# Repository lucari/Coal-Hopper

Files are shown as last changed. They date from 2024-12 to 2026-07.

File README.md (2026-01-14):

# Coal-Hopper
This is an Arduino based stepper motor controller for a model railway coal-hopper.

*** The board and software has been updated as more requirements were uncovered. The original files can be found under the V1 folder ***

The design is based around an Arduino Nano and a TMC2209 Silent Stepper motor controller. There are 6 general I/O pins that are used for the home & optional away microswitches, trigger input, busy output, Train detection and Conveyor control. Trimmers are used to set the speed of the hopper, length or travel (if not using Away switch) and delay time at the Away position before moving home.

Note. The 5v supply on the I/O pins comes from the Nano voltage regulator. It will not be enough to drive relays and servos. In this instance, an external power source is required.

The end-stop switches can be Normally-Open or Normally Closed types and set by configuration variables in the software. 

When a train is detected (reed switch), the conveyor motor, via a relay board, is turned on for a period of time.

When triggered by the level of coal in the hopper or the train leaving the unloading section, and after a delay, the stepper motor will move the hopper to the Away position. Once at the top and after a delay (when the hopper is emptied), the hopper will move back to the Home position. During this time, the busy output is used via a relay to disable track power in the unloading section. 

At initialisation time, the hopper is moved back to Home. If the hopper is already Home, it is moved away for a few turns and then back Home.

The Arduino will normally be powered through the Stepper Motor supply. There is a jumper provided so this can be isolated if the Arduino is connected by its USB port to a PC. This will avoid conflicting power on the Nano.

## Arduino Code
The code is held under the Arduino folder. Any changes to the connections can be made at the top of the file. The code is written 'long-hand' to make it readable and maintainable.

## Kicad Files
A Custom PCB was made for this and can be found under the Kicad folder.

Image of the PCB Front
Image of the PCB Rear

## Completed Boards
The image below shows a completed board. 

Image of PCB Built

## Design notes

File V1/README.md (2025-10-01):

# Coal-Hopper
This is an Arduino based stepper motor controller for a model railway coal-hopper.

These are the original files before the new board was created.

When triggered, the stepper motor will move the hopper to the Away position. After a delay (when the hopper is emptied), the hopper will move back to the Home position.

The design is based around an Arduino Nano and TMC2209 Silent Stepper motor controller. There are connection for end-stop switches, but only the Home switch is required. There are trigger input and busy output connections protected by opto-couplers. These can be removed if required and direct connections used instead (i.e relay / switch for input). Trimmers can be used to set the speed of the hopper, length or travel (if not using Away switch) and delay time at the Away position before moving home.

The end-stop switches can be Normally-Open or Normally Closed types and set by installing a jumper on the appropriate header. For Normally Open types, these can actually be left off but the board has space for the jumpers.

The Arduino can also be powered through the Motor supply. There is a jumper provided so this can be isolated if the Arduino is connected by its USB port to a PC. Its stops strange things happening.

## Arduino Code
The code is held under the Arduino folder. Any changes to the connections can be made at the top of the file. The code is written 'long-hand' to make it readable and maintainable.

## Kicad Files
A Custom PCB was made for this and can be found under the Kicad folder.

Image of the PCB Front
Image of the PCB Rear

## Completed Boards
The images below show completed boards. 
This one has the Opto-Couplers installed.

Image of PCB with Opto-Couplers

This one has direct links and can be used for relay contacts or switch. It also has headers for the LEDs so they can be mounted remotely.

Image of PCB with Opto-Couplers

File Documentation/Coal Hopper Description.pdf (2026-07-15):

# Coal Hopper

# Design Notes

## Version 1.0

Coal Hopper Design v1.0

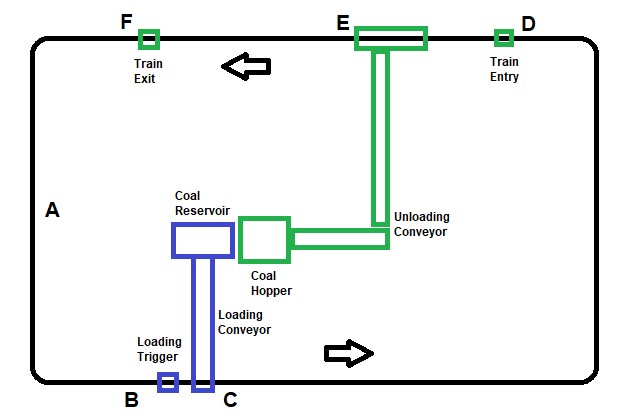
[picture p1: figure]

Page 1 of 9

## Overview

The Coal Wagon exhibition layout of the Bracknell Railway Society runs a continuous loop of trains, pulling several coal wagons, that are filled and emptied automatically. A simplified layout is shown below.

The train, pulling a number of coal wagons, travels anti-clockwise starting empty at point A. Each wagon has a small magnet fitted and when it passed over the loading trigger reed switch at point B, it causes the train to stop after a short delay, with the wagon under the loading chute C. This also starts the loading conveyor to move coal from the reservoir into a loading bucket. When this fills to a certain amount, the bucket tips and dispenses the coal down the chute into the wagon. A tilt switch on the bucket stops the conveyor and after a short delay, restarts the train. As each wagon passes the loading trigger, the process repeats. When all the wagons are loaded, the train continues around the loop.

When the train reaches train entry point D, the unloading conveyor is started. As the wagons reach point E, the coal is automatically unloaded through the bottom of the wagon. The coal is moved up the unloading conveyors to the coal hopper.

Once the train reaches the train exit point F, and after a short delay, the unloading conveyor is turned off. The coal hopper is raised up the tower and is tipped into the coal reservoir. It then returns to the base.

The train reaches point A again and the cycle repeats itself.

This document covers the green unloading part of the layout and how the reservoir of coal in the loading tower is replenished.

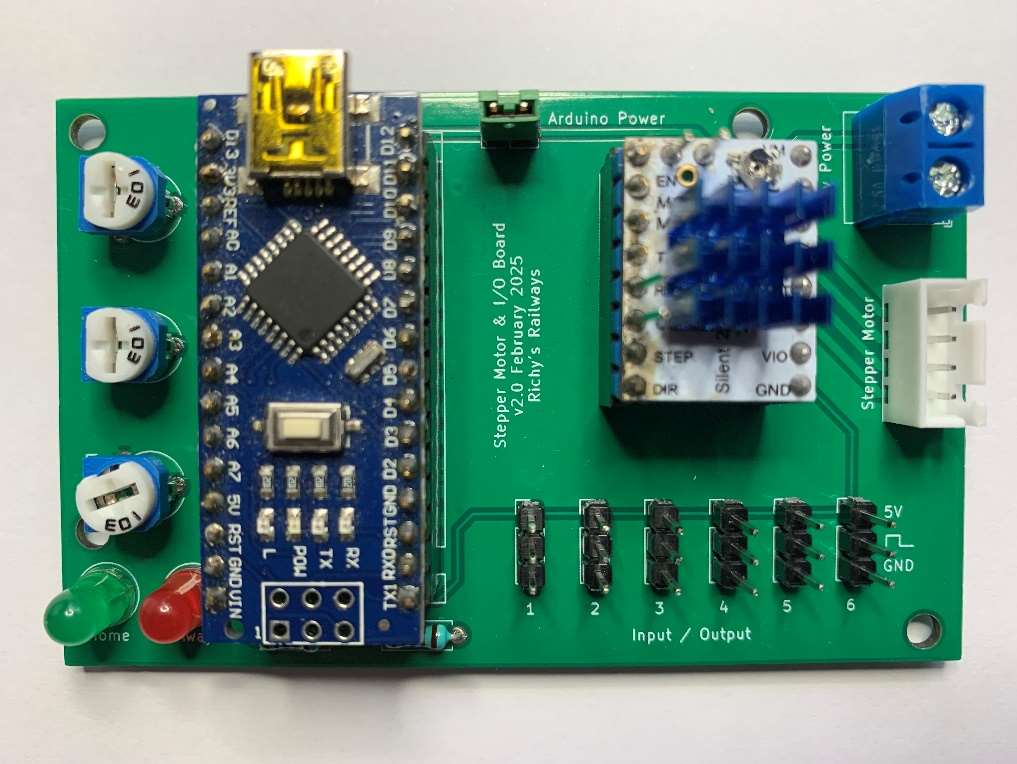
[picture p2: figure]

Page 2 of 9

## Hardware

A custom PCB has been designed, based on an Arduino microcontroller that detects the train location and moves a coal hopper lift using a stepper motor. The final version of the board is shown below.

The main part of the board is the Arduino Nano. The USB interface on this is used only for programming and debugging. In normal operation, it takes power from the 12V supply used for the Stepper Motor.

The jumper to the right of the Arduino can be used to disconnect the 12V supply. When the Arduino is powered through its USB connector, the jumper should be removed to avoid power supply conflicts and protect the host computer. In normal; operation with no USB connection, the jumper should be fitted.

The stepper motor driver is a Silent_2209 board. This drives the stepper motor in 1/8 micro steps with very little noise compared to a normal driver board.

The 3 variable resisters or trimmers are used to tune the configuration of the board. These are:

- Delay – the time to wait before moving to the home or away position.
- Speed – How fast the stepper motor turns.
- Length – The number of turns the motor will take to move from home to away.

Page 3 of 9

There are 6 I/O interfaces on the board. These are used as follows:

1. Home switch (input) – This is connected to a ‘normally-open’ microswitch.
2. Away switch (input) – This is currently not fitted.
3. Conveyor motor control (output) – This drives a relay board.
4. Train entry sensor (input) – This is a small reed switch.
5. Train exit sensor (input) – This is a small reed switch.
6. Busy / Track power (output) – This drives a relay board.

The two LEDs display different patterns depending on what state the board is in.

The Green LED shows the ‘Home’ state, and the Red LED shows the ‘Away’ state. These will light and flash in different combinations to show what function the board is performing.

All the above will be covered in detail within the document.

Page 4 of 9

## Software Description

The Arduino code is written in ‘C’ and can be found in the GitHub repository at https://github.com/lucari/Coal-Hopper, along with the PCB design files. The code should be used with the following description to understand how it works.

The software design is based on a finite-state-machine model. The code will be in one state until some trigger causes it to perform an action and move to a new state. The possible states are: Initialise, Home, Move-Away, Away, Move-Home and Error.

Initialise

Once the Arduino starts up and has performed its local setup functions, it is in the Initialise state (InitialiseHopper function). It flashes the LEDs to show test they are working and reads the trimmer pots to get the tuneable values.

Because the power could have been removed at any time, the location of the hopper is checked. If the home switch is active (hopper is home), then it is moved away for a number of turns and then returned home. If the Home switch is inactive (hopper is away), the hopper is returned home. This checks that the home switch is working correctly. If the state of the home switch does not change after a number of turns, the program enters the Error state. If the home switch does change correctly, the program enters the Home state.

Home

This is the state that the program will be in most of the time (WaitForHopperTrigger function). The stepper motor is disabled during this time to save power. While it is idle, it will check the trimmer pots every 15 seconds and update the tuneable values.

The function is waiting for one of two triggers to occur. The ‘Train Entry’ trigger (trainSensorPin) going low cause the unloading conveyors to start. This is handled by taking the conveyorMotorPin pin low, which is connected to an external relay board. It also starts a 60 second time that is checked within the loop. When this expires, the pin is raised and stopping the conveyors. The state is not changed by this event.

When the ‘Train Exit’ trigger (bucketFullSensorPin) goes low, the idle loop is exited. The program will wait for the number of seconds defined by the trim pots. This is to ensure that the unloading conveyors are empty and the train has cleared the section. The track power is then turned off by taking the hopperBusyPin pin low. This is connected to an external relay board. It also stops the unloading conveyors if they were running. The program enters the Move-Away state.

Page 5 of 9

Move-Away

This is the transient state where the hopper is being moved from the home (lower) to the away (raised) position (MoveHopperToAway function). The stepper motor board is driven by setting the direction pin high and the enable pin low. The step pin is pulsed by setting it high, wait, low, and wait. The wait time is set by the trimmer pots, and the optimum value was found to be 200uS. At the start and end of the run, the delay is doubled to slow it down.

It was found that a steady stream of pulses works best. When the debug messages were included, the stepper produced a knocking sound at each turn. So, these have been commented out.

The stepper motor is moved until the away switch is reached (if fitted) or the number of turns specified by the trim pots is reached. The number of turns required on the current setup is 53. The driver board is set for 1/8 steps so a full turn will require 8 * 200 = 1600 pulses.

When the endpoint is reached, the stepper motor is disabled to save power. The program enters the Away state.

Away

This is the transient state when the hopper is at the highest point and is emptying the coal into the reservoir (WaitForHopperToEmpty function). It simply waits for the number of seconds defined by the trimmer pots. The value of 10 seconds seems to work best.

Once the timer expires, the program enters the Move-Home state.

Move-Home

This is the transient state where the hopper is being moved from the away (raised) to the home (lower) position (MoveHopperToHome function). It operates in the same manner as the Move-Away state, except the direction pin is set low. The Home switch will always be fitted so this is the trigger that will stop the hopper moving. Once reached, the program enters the Home state.

If the number of turns is exceeded, the program enters the Error state.

Error

When something unexpected happens, the program enters the Error state and halts processing.

Page 6 of 9

## LED Patterns / Debugging

The two LEDs show the current state and functions of the program.

Home Green | Away Red | Meaning
On On Off | On Off Off | Initialise / Start up sequence
On Off | Off On | Error state. Alternates every second
On | Off | Home state – waiting for trigger
On | Fast | Home state – delay before moving away (fast flash Away LED)
On | Flash | Move-Away state – alternate Away LED each turn
Off | On | Away state – waiting for timeout
Flash | On | Move-Home – alternate Home LED each turn

The USB port of the Arduino can also be used to view debug messages from the program. The Arduino Power jumper should be removed from the board to avoid conflicts. A USB lead should be connected to a computer and the Arduino IDE started. The Serial Monitor can be found under the Tools menu. The serial port speed should be set to 115200.

InitialiseHopper: Start
InitialiseHopper: Hopper away from home position. Moving to home.
InitialiseHopper: Full turn home complete. InitialiseHopper: Full turn home complete. InitialiseHopper: Full turn home complete. InitialiseHopper: Hopper successfully moved home. WaitForHopperTrigger: At start, waiting 5 seconds. WaitForHopperTrigger: Waiting for trigger to move. WaitForHopperTrigger: Setting defaultDelay (Speed) to 206 WaitForHopperTrigger: Setting turnsToAway (Length) to 53 WaitForHopperTrigger: Setting awayWaitTime (Delay) to 10146

Page 7 of 9

## Connectivity

The connections to the board are shown below. It should be noted that the 5V supply is fed from the Arduino on-board regulator and can only provide limited current. It cannot be used to drive relay boards or servos. The signal side (opto isolator) connection is ok to use 5V, but not the relay side (JD-VCC).

These connections are directly connected.

I/O 1 | Gnd | Black | Home switch direct on green and black wire.
| Sig | Green
| +5V | -
I/O 2 | Gnd | - | Not used
| Sig | -
| +5V | -

These connections are through the patch block.

I/O 3 | Gnd | - | Unload conveyor relay board. Just uses +5V and signal. Relay board must use external
| | Brown | power for relay side (JD-VCC) Sig
| +5V | Red
I/O 4 | Gnd | Orange | Reed switch. Just uses Sig and Gnd.
| Sig | Yellow
| +5V | Green
I/O 5 | Gnd | Blue | Reed switch. Just uses Sig and Gnd.
| Sig | Violet
| +5V | Grey
I/O 6 | Gnd | - | Track Power isolator relay board. Just uses +5V and signal. +5V is common with I/O 3. Relay board must use external power for relay side (JD-VCC)
| Sig | White
| +5V | Black

Page 8 of 9

## Stepper Motor Wiring

It has been found that there are two type of stepper motor interfaces and require different cables. If the wrong cable is used, the stepper motor will judder and not turn.

4 pin (driver) | 6 pin type 1 | 6 pin type 2
| A2 | A2
A2 | - | -
A1 | A1 | B1
B1 | B1 | A1
B2 | - | -
| B2 | B2

The pins on the stepper motor should be checked for connectivity to determine the correct cable.

*** The stepper motor type in the current installation is unknown ***

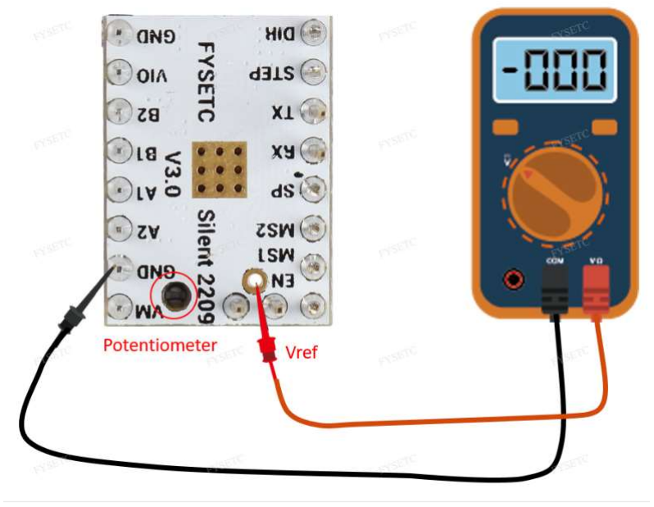
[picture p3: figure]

Page 9 of 9

## Stepper Motor Current Limit

The current limit must be set on the stepper driver board, or it will consume high current and could impact the wiring. The current is set by applying power to the VM and Ground pins and then measuring the voltage on the Vref pin. The current limit can be adjusted using the trim pot. The stepper motor must not be connected to the board, or it will cause damage.

The current is defined as Vref * 0.71. The board is set to 0.6A with a Vref of 0.85V

The weblink https://wiki.fysetc.com/docs/Silent2209 gives full details of the stepper motor driver board.

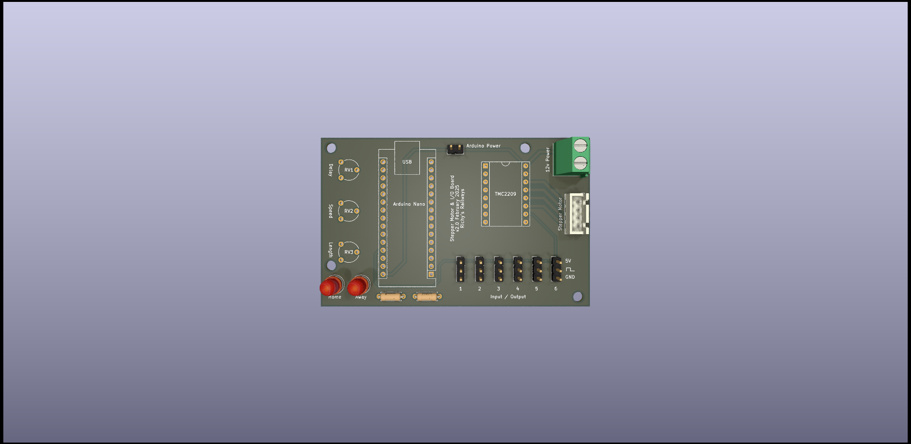
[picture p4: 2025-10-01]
Kicad/Coal-Hopper-V2.png

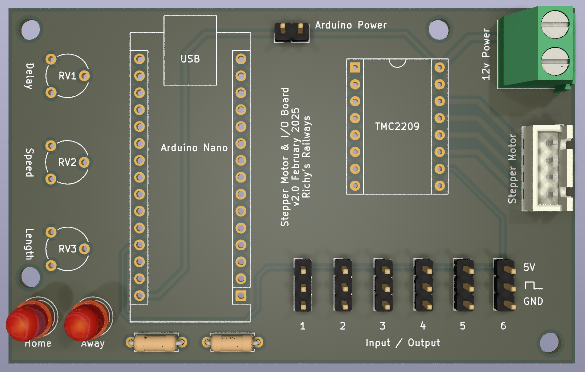
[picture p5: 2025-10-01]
Kicad/Coal-Hopper-V2-cropped.png

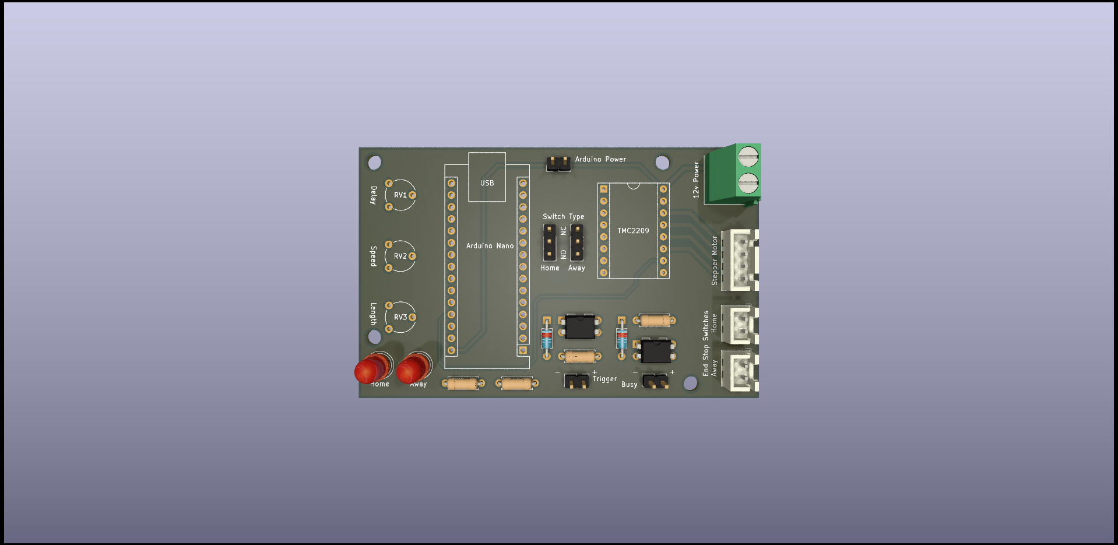
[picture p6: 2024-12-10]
V1/Kicad/Coal-Hopper.png

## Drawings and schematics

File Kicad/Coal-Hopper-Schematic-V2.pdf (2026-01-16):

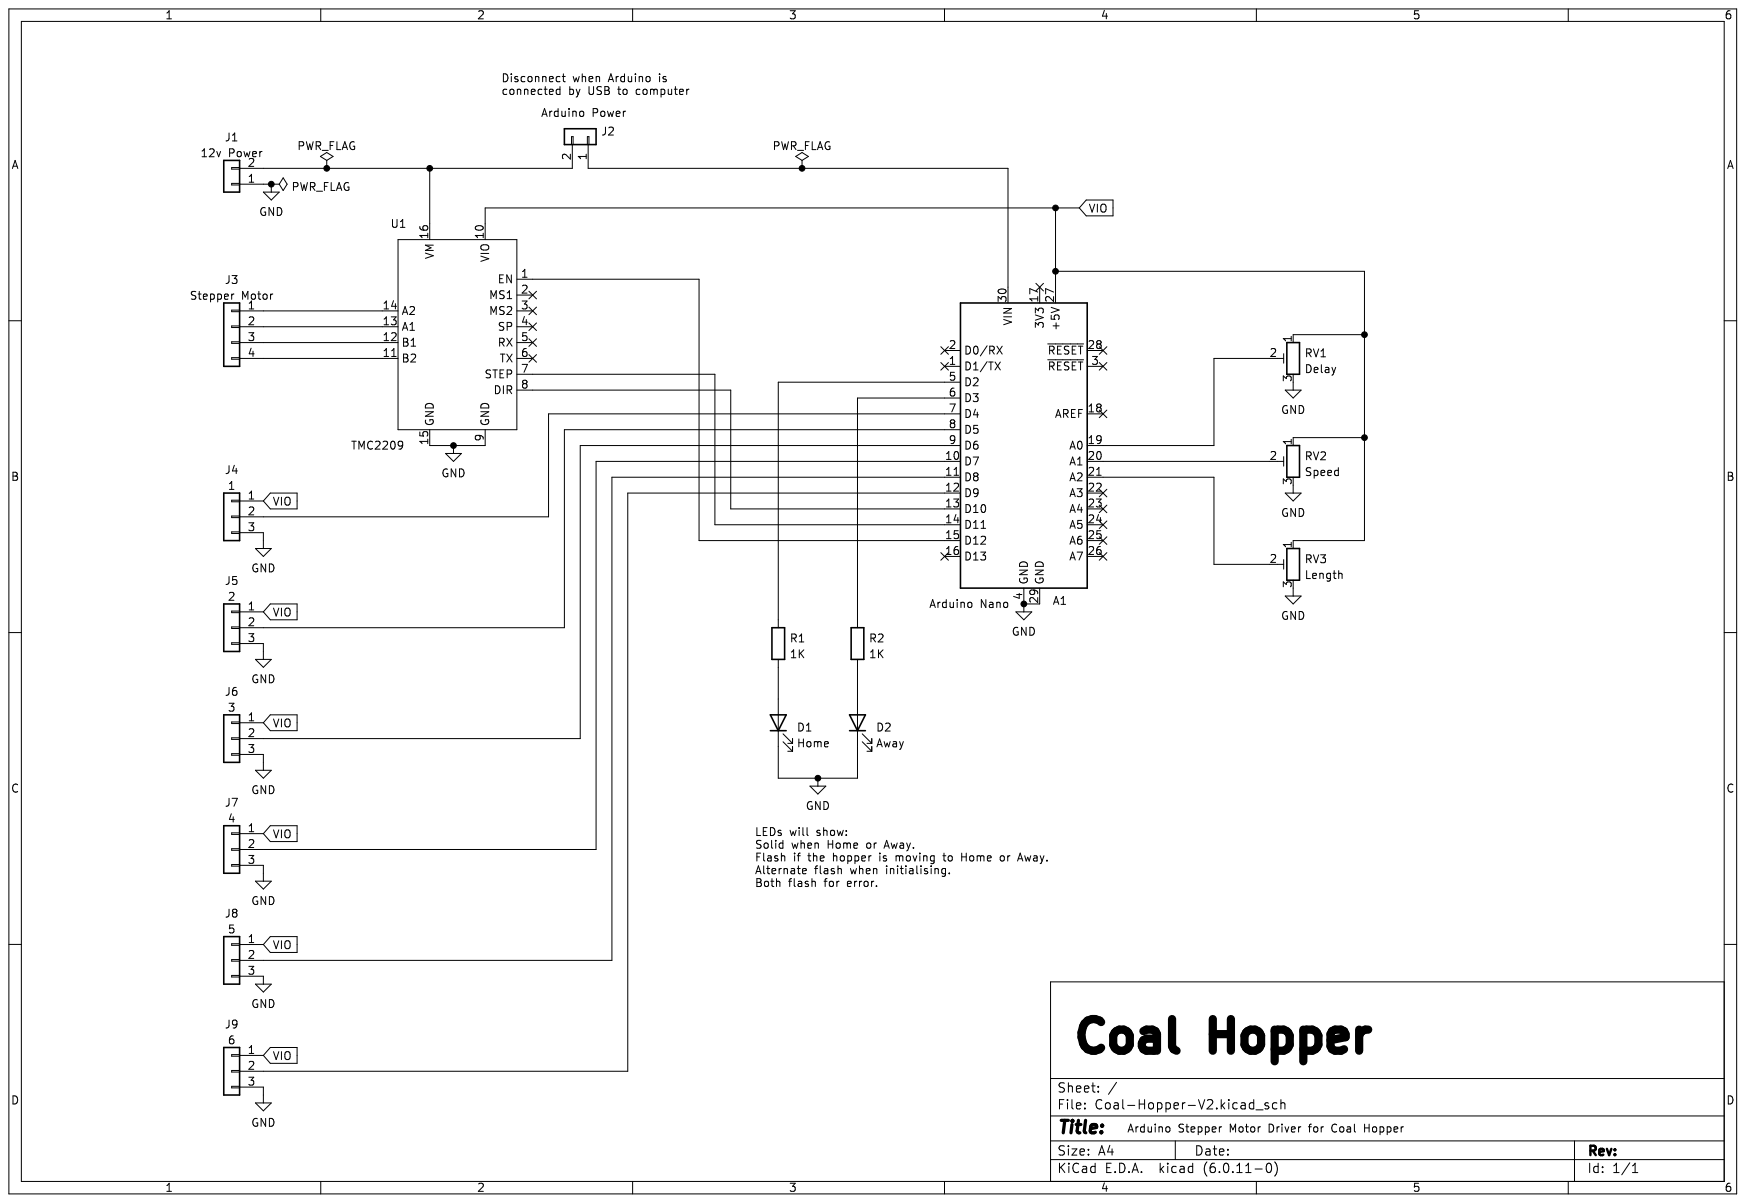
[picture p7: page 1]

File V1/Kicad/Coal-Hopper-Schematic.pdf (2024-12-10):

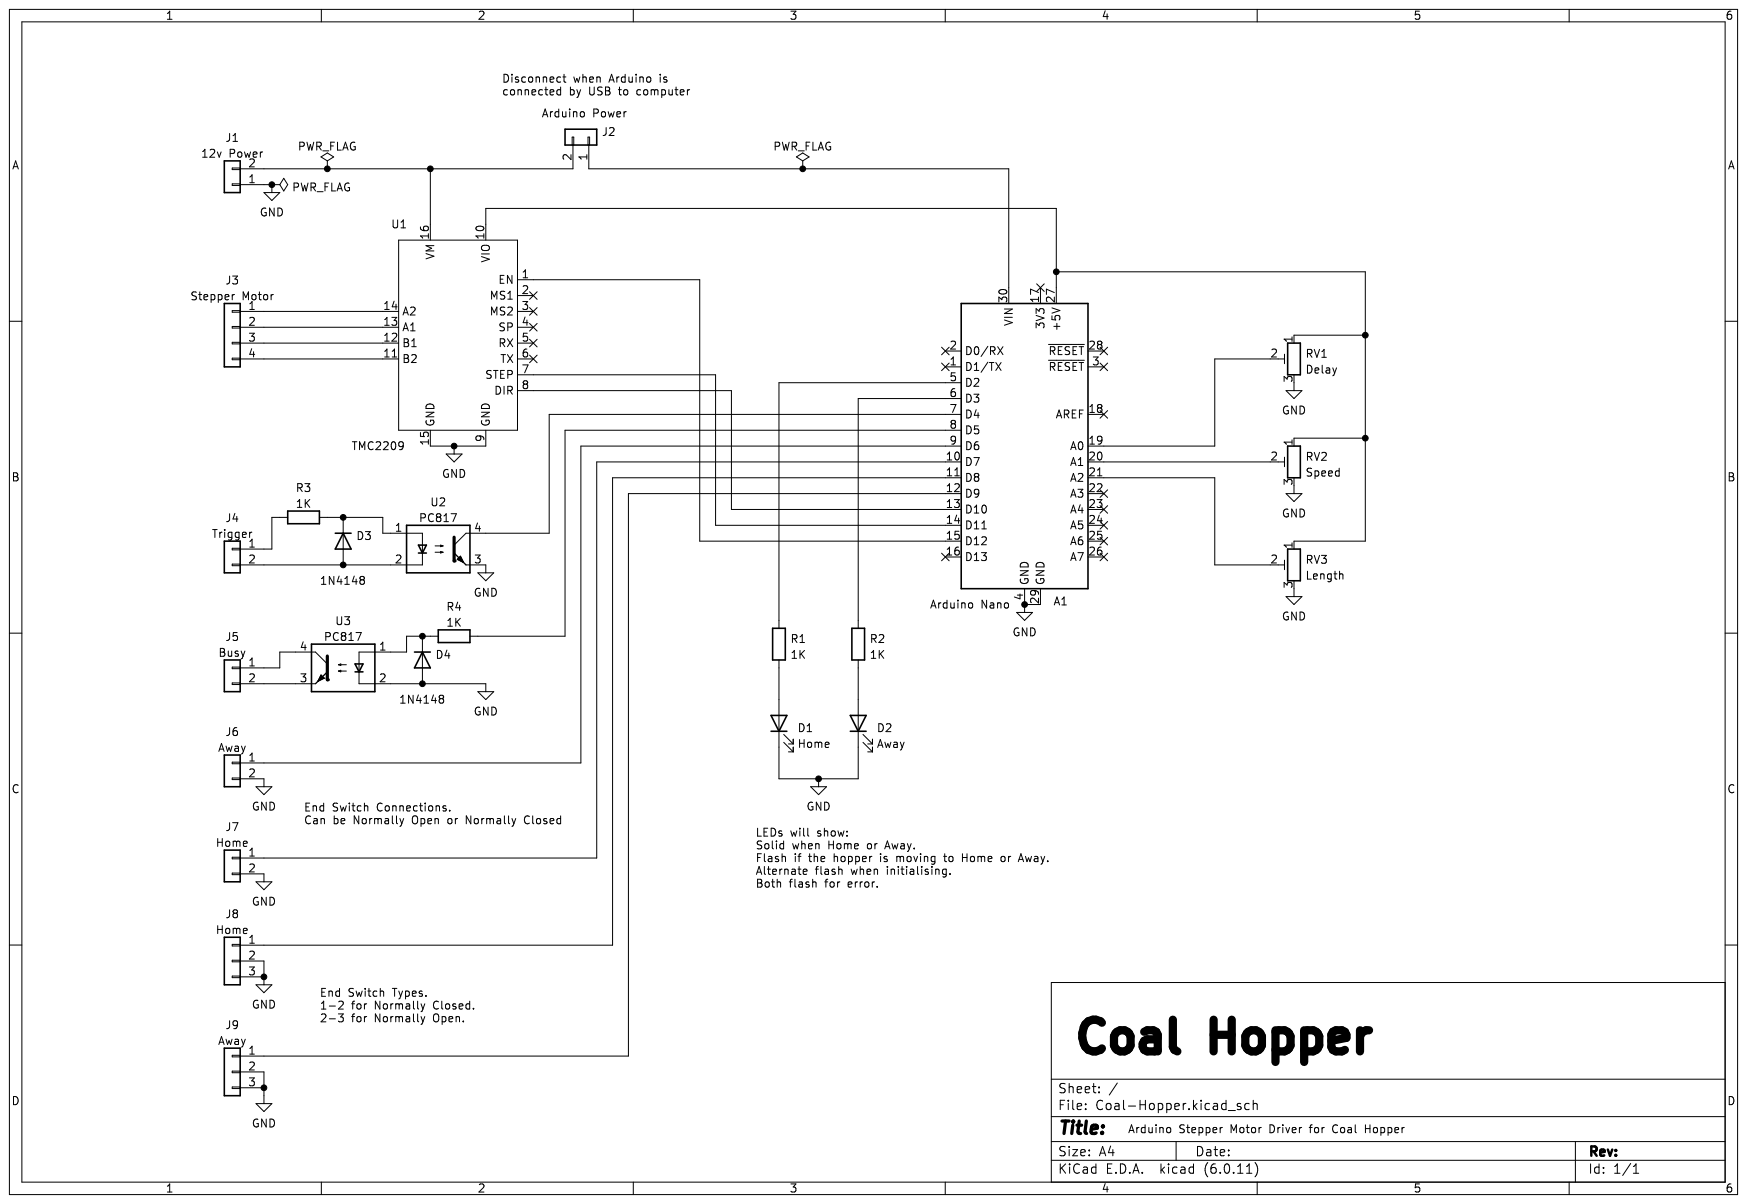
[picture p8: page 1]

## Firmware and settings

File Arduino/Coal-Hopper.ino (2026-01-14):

// Coal Hopper Stepper Functions
//
// Arduino code to control the movement of a coal hopper for a model railway layout.
// 
// Version History
//
// v1.0 07/11/2024 First draft
// v2.0 10/11/2024 Some minor tweaks
// v3.0 20/11/2024 Added Analog inputs for Speed, Wait and Length. 
// v4.0 10/12/2024 Reconfigure for new PCB
// v5.0 07/07/2025 Reconfigure for updated PCB
// v6.0 07/11/2025 Added delay on trigger to allow coal to clear conveyor before moving bucket.
//


//======== The following can be changed to suit the setup ===========================

// Define stepper motor connections
#define homeLEDPin 2
#define awayLEDPin 3

#define homePin 4
#define awayPin 5
#define conveyorMotorPin 6
#define trainSensorPin 7
#define bucketFullSensorPin 8
#define hopperBusyPin 9

#define directionPin 10
#define stepPin 11
#define enablePin 12


// Define Analog pins
#define delayAnalog A0
#define speedAnalog A1
#define lengthAnalog A2

// Define steps per revolution and size of travel
#define stepsPerRevolution (8 * 200)

// We always use the home switch so this is fixed for 500mm
#define MAX_TURNS_TO_HOME 55

#define DEFAULT_TURNS_TO_AWAY 40
#define MIN_TURNS_TO_AWAY 35
#define MAX_TURNS_TO_AWAY 55

// Specify if Home switch is Normally Open or Closed
#define DEFAULT_HOME_OPEN true 

// Specify if Away switch is Normally Open or Closed
#define DEFAULT_AWAY_OPEN true 

// Specify if Hopper Triger is Active High or Low 
#define TRIGGER_ACTIVE_HIGH false 

// Specify if Train Sensor is Active High or Low 
#define TRAINSENSOR_ACTIVE_HIGH false

// Specify the default delay between steps in uS (will be double this) amd the max & min
#define DEFAULT_DELAY 200
#define MIN_DELAY 100
#define MAX_DELAY 300

// Specify the default wait time in mS at the top
#define DEFAULT_WAIT 10000
#define MIN_WAIT 5000
#define MAX_WAIT 15000


//===================================================================================


// Define the states the hopper can be in
#define HOPPER_INIT 0
#define HOPPER_HOME 1
#define HOPPER_MOVE_AWAY 2
#define HOPPER_AWAY 3
#define HOPPER_MOVE_HOME 4
#define HOPPER_ERROR 255


// Define if the motor is going to Home or Away
#define STEP_AWAY 0
#define STEP_HOME 1


// Set state to init
int hopperState = HOPPER_INIT;

// Set delay to 200uS
int defaultDelay = DEFAULT_DELAY;

// Set the default distance to away until we read the triimers
int turnsToAway = DEFAULT_TURNS_TO_AWAY;

// Set the time to wait at the top before returning / time after trigger that we wait for before moving the hopper.
int awayWaitTime = DEFAULT_WAIT;

// Set a flag to ignore trimmers if all analog inputs are grounded
bool checkTrimmers = true;

// Variables to specify if home and away switch are normally open or closed. 
bool awaySwitchNO = DEFAULT_AWAY_OPEN;
bool homeSwitchNO = DEFAULT_HOME_OPEN;

// Conveyor will run for 60 seconds
#define CONVEYOR_RUN_TIME 60000L
unsigned long stopConveyorTime = 0L;

// Declare functions
void InitialiseHopper();
void WaitForHopperTrigger();
void MoveHopperToAway();
void WaitForHopperToEmpty();
void MoveHopperToHome();
void HopperError();
bool IsHomeActive();
bool IsAwayActive();
bool IsTriggerActive();

void setup() 
{
  // Declare pins as output:
  pinMode(stepPin, OUTPUT);
  pinMode(directionPin, OUTPUT);
  pinMode(enablePin, OUTPUT);
  pinMode(hopperBusyPin, OUTPUT);
  pinMode(conveyorMotorPin, OUTPUT);
  pinMode(homeLEDPin, OUTPUT);
  pinMode(awayLEDPin, OUTPUT);

  // and the inputs with pullups
  pinMode(homePin, INPUT_PULLUP);
  pinMode(awayPin, INPUT_PULLUP);
  pinMode(trainSensorPin, INPUT_PULLUP);
  pinMode(bucketFullSensorPin, INPUT_PULLUP);

  // Disable the controller for now
  digitalWrite(enablePin, HIGH);

  // Show we are busy and converyor off (relays active low)
  digitalWrite(hopperBusyPin, LOW);
  digitalWrite(conveyorMotorPin, HIGH);

  // Clear the LEDs
  digitalWrite(homeLEDPin, LOW);
  digitalWrite(awayLEDPin, LOW);

  // Configure Serial for debugging
  Serial.begin(115200);

  // Give it time to settle
  delay(500);

  // Set the initial state to init.
  hopperState = HOPPER_INIT;
}

void loop()
{
  // Loop around and call the appropriate function delepnding on the state.
  if (hopperState == HOPPER_INIT)
  {
    // First thing is to initialise and home the hopper
    InitialiseHopper();
  }
  else if (hopperState == HOPPER_HOME)
  {
    // Hopper is Home, wait to be told to move the hopper
    WaitForHopperTrigger();
  }
  else if (hopperState == HOPPER_MOVE_AWAY)
  {
    // Move the hopper to the away point
    MoveHopperToAway();
  }
  else if (hopperState == HOPPER_AWAY)
  {
    // Hopper is away, wait for it to empty.
    WaitForHopperToEmpty();
  }
  else if (hopperState == HOPPER_MOVE_HOME)
  {
    // Move the hopper back home
    MoveHopperToHome();
  }
  else
  {
    // Something has broken. Stop
    HopperError();
  }
}



bool
IsTriggerActive()
{
  // Check to see if its active high or low
  if (TRIGGER_ACTIVE_HIGH)
  {
    // It is active high
    if (digitalRead(bucketFullSensorPin) == HIGH)
    {
      return(true);
    }
    else
    {
      return(false);
    }
  }
  else
  {
    // It is active low
    if (digitalRead(bucketFullSensorPin) == LOW)
    {
      return(true);
    }
    else
    {
      return(false);
    }    
  }
}

bool
IsTrainSensed()
{
  // Check to see if its active high or low
  if (TRAINSENSOR_ACTIVE_HIGH)
  {
    // It is active high
    if (digitalRead(trainSensorPin) == HIGH)
    {
      return(true);
    }
    else
    {
      return(false);
    }
  }
  else
  {
    // It is active low
    if (digitalRead(trainSensorPin) == LOW)
    {
      return(true);
    }
    else
    {
      return(false);
    }    
  }
}

//
// Is Home Switch Active
//
// Checks the state of the home switch.
// Caters for Normally Open and Normally Closed type switches
// Switch is between pin and ground with pullup enabled
//
bool
IsHomeActive()
{
  if (homeSwitchNO)
  {
    // Home switch is normally open
    if (digitalRead(homePin) == LOW)
    {
      // Active low so switch is pressed (NO)
      return(true);
    }
    else
    {
      // Its high, so not switched (NO)
      return(false);
    }
  }
  else
  {
    // Home switch is normally closed
    if (digitalRead(homePin) == LOW)
    {
      // Active low so its not switched (NC)
      return(false);
    }
    else
    {
      // Its high, so switch is pressed (NC)
      return(true);
    }
  }
}

//
// Is Away Switch Active
//
// Checks the state of the away switch.
// Caters for Normally Open and Normally Closed type switches
// Switch is between pin and ground with pullup enabled
//
bool
IsAwayActive()
{
  if (awaySwitchNO)
  {
    // Away switch is normally open
    if (digitalRead(awayPin) == LOW)
    {
      // Active low so switch is pressed (NO)
      return(true);
    }
    else
    {
      // Its high, so not switched (NO)
      return(false);
    }
  }
  else
  {
    // Away switch is normally closed
    if (digitalRead(awayPin) == LOW)
    {
      // Active low so its not switched (NC)
      return(false);
    }
    else
    {
      // Its high, so switch is pressed (NC)
      return(true);
    }
  }
}


//
// Move Stepper
//
// Move the stepper one step to Home or Away and wait.
//
void
MoveStepper(int stepDirection, int stepDelay)
{
  // Enable the board
  digitalWrite(enablePin, LOW);

  // Check direction
  if (stepDirection == STEP_AWAY)
  {
    // Move to Away point
    digitalWrite(directionPin, HIGH);
  }
  else
  {
    // Move to Home point
    digitalWrite(directionPin, LOW);
  }
  
  // Pulse line high
  digitalWrite(stepPin, HIGH);

  // Wait for passed time (uS)
  delayMicroseconds(stepDelay);
  
  // Pulse line low
  digitalWrite(stepPin, LOW);

  // Wait for passed time (uS)
  delayMicroseconds(stepDelay);
 
}


//
// Initialise Hopper
//
// At startup, move hopper back to home position.
// If the hopper is already home, move away and back to confirm switch.
// If the Home switch does not activate after a number of turns, move to ERROR state.
// If ok, set the HOME state.
//
void
InitialiseHopper()
{
  bool ledsAreOn = false;
  
  Serial.print(F("InitialiseHopper: Start\n"));

  // Flash the LEDs at the start so we dont move the motor as soon as the power is applied

  digitalWrite(homeLEDPin, HIGH);
  digitalWrite(awayLEDPin, HIGH);
  delay(2000);
  digitalWrite(homeLEDPin, HIGH);
  digitalWrite(awayLEDPin, LOW);
  delay(2000);
  digitalWrite(homeLEDPin, LOW);
  digitalWrite(awayLEDPin, LOW);
  delay(2000);

  // Check to see if all the analog inputs are grounded. If so, ignore them and use defaults
  if (analogRead(delayAnalog) == 0 && analogRead(speedAnalog) == 0 && analogRead(lengthAnalog) == 0)
  {
    Serial.print(F("InitialiseHopper: All trimmers at 0 so using defaults.\n"));

    Serial.print(F("WaitForHopperTrigger: Setting defaultDelay (Speed) to "));
    Serial.print(defaultDelay);
    Serial.print(F(" \n"));

    Serial.print(F("WaitForHopperTrigger: Setting turnsToAway (Length) to "));
    Serial.print(turnsToAway);
    Serial.print(F(" \n"));

    Serial.print(F("WaitForHopperTrigger: Setting awayWaitTime (Delay) to "));
    Serial.print(awayWaitTime);
    Serial.print(F(" \n"));

    
    checkTrimmers = false;
  }


 
  // First check if the home switch is already active (low)
  if (IsHomeActive() == true)
  {
    Serial.print(F("InitialiseHopper: Hopper at home position. Moving away.\n"));
    // Yes, move away a number of steps (4 rotations) to see if it goes high.
    for (int i = 0; i < 4; i++)
    {

      // Flash the LEDs at the same time
      if (ledsAreOn == true)
      {
        // Its on so turn it off
        ledsAreOn = false;
        digitalWrite(homeLEDPin, LOW);
        digitalWrite(awayLEDPin, LOW);
      }
      else
      {
        // Its off so turn it on
        ledsAreOn = true;
        digitalWrite(homeLEDPin, HIGH);
        digitalWrite(awayLEDPin, HIGH);
      }
      
      for (int j = 0; j < stepsPerRevolution; j++)
      {
        // Move at half speed.
        MoveStepper(STEP_AWAY, defaultDelay*2);        
      }
      Serial.print(F("InitialiseHopper: Full turn away complete.\n"));
    }

    // Check again
    if (IsHomeActive() == true)
    {
      // Its still active so hasn't moved. Go to Error state
      Serial.print(F("InitialiseHopper: *** Error *** Hopper failed to move away.\n"));
      hopperState = HOPPER_ERROR;
      return;
    }
  }

  // If we are here, the home switch must be inactive. Try and move it to Home.
  Serial.print(F("InitialiseHopper: Hopper away from home position. Moving to home.\n"));
  for (int i = 0; i < MAX_TURNS_TO_HOME; i++)
  {

    // Flash the LEDs at the same time
    if (ledsAreOn == true)
    {
      // Its on so turn it off
      ledsAreOn = false;
      digitalWrite(homeLEDPin, LOW);
      digitalWrite(awayLEDPin, LOW);
    }
    else
    {
      // Its off so turn it on
      ledsAreOn = true;
      digitalWrite(homeLEDPin, HIGH);
      digitalWrite(awayLEDPin, HIGH);
    }
    
    for (int j = 0; j < stepsPerRevolution; j++)
    {
      // Check to see if we have hit the home stop
      if (IsHomeActive() == true)
      {
        // Yes. Init is complete
        Serial.print(F("InitialiseHopper: Hopper successfully moved home.\n"));
        hopperState = HOPPER_HOME;
        return;
      }
      
      // Move at half speed.
      MoveStepper(STEP_HOME, defaultDelay*2);        
    }
    Serial.print(F("InitialiseHopper: Full turn home complete.\n"));
  }

  // If we reach here, it means we have not found the Home switch. So throw an error
  Serial.print(F("InitialiseHopper: *** Error *** Hopper failed to move home.\n"));
  hopperState = HOPPER_ERROR;
}


//
// Wait For Hopper Trigger (Home)
//
// Hopper is at home position and waiting for trigger to move.
// When triggered, move to MOVE_AWAY state
//
void
WaitForHopperTrigger()
{
  int count;
  long longScratch1;
  long longScratch2;
  long longScratch3;
  
  // Disable the stepper controller to save power
  digitalWrite(enablePin, HIGH);

  // Turn on Home LED and AWAY off
  digitalWrite(homeLEDPin, HIGH);
  digitalWrite(awayLEDPin, LOW);

  // At start, wait 5 seconds before doing anything
  Serial.print(F("WaitForHopperTrigger: At start, waiting 5 seconds.\n"));
  delay(5000);

  // Show we are not busy
  digitalWrite(hopperBusyPin, HIGH);
  

  Serial.print(F("WaitForHopperTrigger: Waiting for trigger to move.\n"));

  // Keep track of how long we wait so we can read trimmers. First time read them at the start
  count = 0;
  
  // Check the trigger
  while(IsTriggerActive() == false)
  {
    // Check the train sensor
    if (IsTrainSensed())
    {
      // Yes, start the conveyor and start timer
      Serial.print(F("WaitForHopperTrigger: Train Sensed, Starting Conveyor.\n"));
      
      digitalWrite(conveyorMotorPin, LOW);
      stopConveyorTime = millis() + CONVEYOR_RUN_TIME;
    }

    // Check conveyor timer
    if (stopConveyorTime > 0L)
    {
      if (millis() > stopConveyorTime)
      {
        Serial.print(F("WaitForHopperTrigger: Conveyor Timer expired, Stopping Conveyor.\n"));
        
        digitalWrite(conveyorMotorPin, HIGH);
        stopConveyorTime = 0L;
      }
    }
    // Sleep for 1/100 second if not
    delay(10);
    --count;
    
    // Timed out for trimmers if enabled
    if (checkTrimmers && count < 0)
    {
      // Set to wait 15 seconds before reading again
      count = 1500;
      
      // Set delay time to govern speed of hopper (Speed Trimmer)
      // Bigger than int values so work it out long hand or it doesnt work very well.
      longScratch1 = MAX_DELAY - MIN_DELAY;
      longScratch2 = longScratch1 * analogRead(speedAnalog);
      longScratch3 = longScratch2 / 1024L;
      defaultDelay = int(longScratch3) + MIN_DELAY;
      Serial.print(F("WaitForHopperTrigger: Setting defaultDelay (Speed) to "));
      Serial.print(defaultDelay);
      Serial.print(F(" \n"));

      // Set how many turns to away (Length Trimmer)
      turnsToAway = (((MAX_TURNS_TO_AWAY - MIN_TURNS_TO_AWAY) * analogRead(lengthAnalog)) / 1024) + MIN_TURNS_TO_AWAY;
      Serial.print(F("WaitForHopperTrigger: Setting turnsToAway (Length) to "));
      Serial.print(turnsToAway);
      Serial.print(F(" \n"));

      // Set the time to wait at the top before returning. (Delay Trimmer)
      // Bigger than int values so work it out long hand or it doesnt work.
      longScratch1 = MAX_WAIT - MIN_WAIT;
      longScratch2 = longScratch1 * analogRead(delayAnalog);
      longScratch3 = longScratch2 / 1024L;
      awayWaitTime = int(longScratch3) + MIN_WAIT;

      Serial.print(F("WaitForHopperTrigger: Setting awayWaitTime (Delay) to "));
      Serial.print(awayWaitTime);
      Serial.print(F(" \n"));
      
    }
  }

  // We have been triggered. Wait before moving. Flash Away LED fast
  Serial.print(F("WaitForHopperTrigger: Got Trigger, Waiting before moving away.\n"));
  Serial.print(F("WaitForHopperTrigger: Sleeping for "));
  Serial.print(awayWaitTime);
  Serial.print(F(" mS\n"));

  // Turn off Away LED
  digitalWrite(awayLEDPin, LOW);

  // Wait for the defined time and toggle the Away LED every 200mS to show something is happening
  count = 0;
  while (count < awayWaitTime)
  {
    delay(200);
    digitalWrite(awayLEDPin, HIGH);
    delay(200);
    digitalWrite(awayLEDPin, LOW);
    count += 400;
  }
  // Turn off Away LED
  digitalWrite(awayLEDPin, LOW);

  // Now we can move the hopper
  Serial.print(F("WaitForHopperTrigger: Got Trigger, state changed to Move-Away.\n"));

  // Turn off Home LED
  digitalWrite(homeLEDPin, LOW);

  // Show we are busy
  digitalWrite(hopperBusyPin, LOW);

  // Stop the conveyor & timer
  digitalWrite(conveyorMotorPin, HIGH);
  stopConveyorTime = 0L;

  hopperState = HOPPER_MOVE_AWAY;
}



//
// Move Hopper to Away position
//
// Trigger has been received and hopper is moved away.
// The speed to of the hopper is ramped up at the start and slowed down as the end.
// Hopper will stop when it hits the Away switch.
// At end, move to AWAY state.
//
void
MoveHopperToAway()
{
  long stepCount = 0;
  int  awayDelayTime;
  bool awayLEDIsOn = false;
  
  Serial.print(F("MoveHopperToAway: Moving Hopper to away point.\n"));

  for (int i = 0; i < turnsToAway; i++)
  {
    // Start off at half speed for a few turns and then normal speed until 75% and then back to half
    if ((i < 2) || (i > (turnsToAway * 0.75)))
    {
      awayDelayTime = defaultDelay*2;
    }
    else
    {
       awayDelayTime = defaultDelay;
    }

    // Flash the LED each turn
    if (awayLEDIsOn == true)
    {
      // Its on so turn it off
      awayLEDIsOn = false;
      digitalWrite(awayLEDPin, LOW);
    }
    else
    {
      // Its off so turn it on
      awayLEDIsOn = true;
      digitalWrite(awayLEDPin, HIGH);
    }


    for (int j = 0; j < stepsPerRevolution; j++)
    {
      // Check to see if we have hit the away stop
      if (IsAwayActive() == true)
      {
        // Yes. move is complete
        Serial.print(F("MoveHopperToAway: Hopper hit away switch.\n"));
        Serial.print(F("MoveHopperToAway: Hopper successfully moved away.\n"));
        Serial.print(F("MoveHopperToAway: "));
        Serial.print(stepCount);
        Serial.print(F(" steps taken.\n"));
        hopperState = HOPPER_AWAY;
        return;
      }

      MoveStepper(STEP_AWAY, awayDelayTime);  
      ++stepCount;      
    }

    // *** Oddly, with this debug code added, the motor clicks every turn ***
    //Serial.print(F("MoveHopperToAway: Full turn away complete.\n"));
    //Serial.print(F("MoveHopperToAway: Delay was "));
    //Serial.print(awayDelayTime);
    //Serial.print(F("uS\n"));
  }

  // If we reach here, it means we have made the requested number of turns. This may be less than the end switch so is ok.
  Serial.print(F("MoveHopperToAway: Hopper moved requested turns.\n"));
  Serial.print(F("MoveHopperToAway: Hopper successfully moved away.\n"));
  Serial.print(F("MoveHopperToAway: "));
  Serial.print(stepCount);
  Serial.print(F(" steps taken.\n"));
  hopperState = HOPPER_AWAY;
  return;
}


//
// Wait for Hopper to empty (AWAY)
//
// Sleeps for a short period to ensure hopper is empty.
// Next state is MOVE_HOME
// 
void
WaitForHopperToEmpty()
{
  // Disable the stepper controller to save power
  digitalWrite(enablePin, HIGH);

  // Turn on the LED
  digitalWrite(awayLEDPin, HIGH);
  
  // Sleep for a while 
  Serial.print(F("WaitForHopperToEmpty: Sleeping for "));
  Serial.print(awayWaitTime);
  Serial.print(F(" mS\n"));
  delay(awayWaitTime);

  // Turn off the LED
  digitalWrite(awayLEDPin, LOW);

  // Then move home
  Serial.print(F("WaitForHopperToEmpty: Moving to Home\n"));
  hopperState = HOPPER_MOVE_HOME;
}


//
// Move hoppper to Home position
//
// Hopper is emptied and moved home.
// The speed to of the hopper is ramped up at the start and slowed down as the end.
// Hopper will stop when it hits the Home switch.
// At end, move to HOME state.
//
void
MoveHopperToHome()
{
  long stepCount = 0;
  int  homeDelayTime;
  bool homeLEDIsOn = false;
  
  Serial.print(F("MoveHopperToHome: Moving Hopper to home point.\n"));

  for (int i = 0; i < MAX_TURNS_TO_HOME; i++)
  {
    // Start off at half speed for a few turns and then normal speed until 75% and then back to half
    if ((i < 4) || (i > (MAX_TURNS_TO_HOME * 0.75)))
    {
      homeDelayTime = defaultDelay*2;
    }
    else
    {
       homeDelayTime = defaultDelay;
    }

    // Flash the LED each turn
    if (homeLEDIsOn == true)
    {
      // Its on so turn it off
      homeLEDIsOn = false;
      digitalWrite(homeLEDPin, LOW);
    }
    else
    {
      // Its off so turn it on
      homeLEDIsOn = true;
      digitalWrite(homeLEDPin, HIGH);
    }

    for (int j = 0; j < stepsPerRevolution; j++)
    {
      // Check to see if we have hit the home stop
      if (IsHomeActive() == true)
      {
        // Yes. move is complete
        Serial.print(F("MoveHopperToHome: Hopper successfully moved home.\n"));
        Serial.print(F("MoveHopperToHome: "));
        Serial.print(stepCount);
        Serial.print(F(" steps taken.\n"));

        // Turn off the LED
        digitalWrite(homeLEDPin, LOW);

        hopperState = HOPPER_HOME;
        return;
      }

      MoveStepper(STEP_HOME, homeDelayTime);  
      ++stepCount;      
    }
    // *** Oddly, with this debug code added, the motor clicks every turn ***
    //Serial.print(F("MoveHopperToHome: Full turn home complete.\n"));
    //Serial.print(F("MoveHopperToHome: Delay was "));
   // Serial.print(homeDelayTime);
   // Serial.print(F("uS\n"));
  }

  // If we reach here, it means we have not found the Away switch. So throw an error
  Serial.print(F("MoveHopperToHome: *** Error *** Hopper failed to trigger home switch.\n"));
  hopperState = HOPPER_ERROR;  
}


//
// Error state
//
// Something has gone wrong. Kill the power and flash the Error LED.
// Possibly retry after a time ???
//
void
HopperError()
{
  Serial.print(F("HopperError: Waiting for Reset.\n"));

  // Disable the controller
  digitalWrite(enablePin, HIGH);

  // Show we are busy 
  digitalWrite(hopperBusyPin, LOW);

  // loop forever until reset
  while(true)
  {
    // flash the LEDs alternatly
    digitalWrite(homeLEDPin, HIGH);
    digitalWrite(awayLEDPin, LOW);
    delay(1000);
    digitalWrite(homeLEDPin, LOW);
    digitalWrite(awayLEDPin, HIGH);
    delay(1000);
    
  }
}

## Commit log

2025-10-01 Update and rename Arduino/Coal-Hopper.ino to V1/Arduino/Coal-Hopper.ino
2026-01-14 Added delay after trigger for coal to clear conveyor
2026-01-14 Added delay after trigger before moving bucket
2026-01-16 PDF of Coal Hopper Schematic
